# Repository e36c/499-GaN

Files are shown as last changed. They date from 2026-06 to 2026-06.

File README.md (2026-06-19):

# GaN Motor Driver
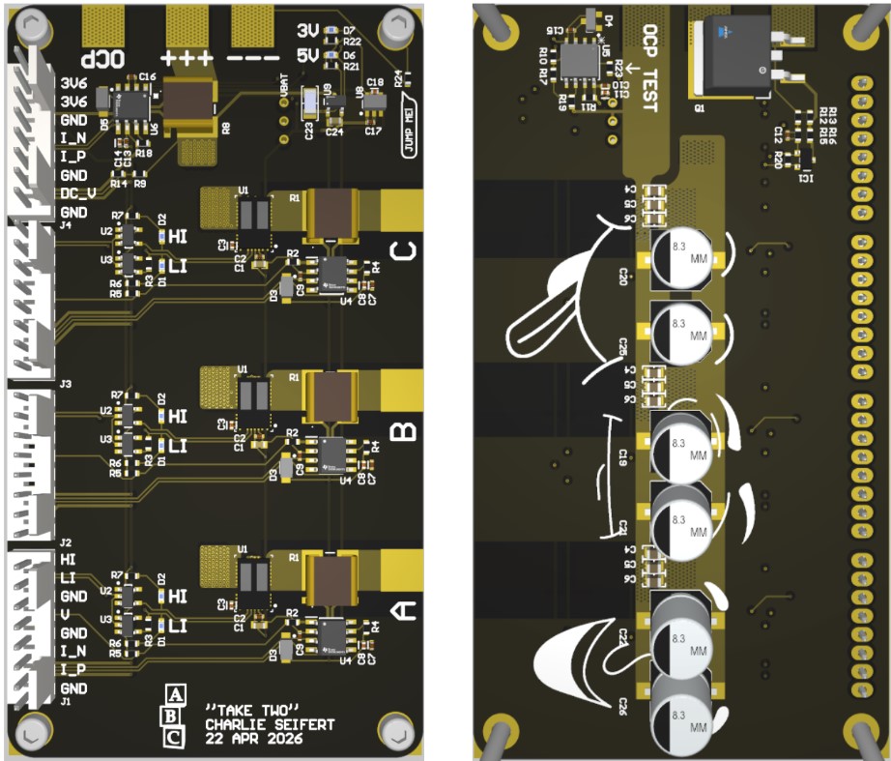
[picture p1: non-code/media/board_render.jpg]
PCB render


This repo contains the design files, code, and final report for my work on a GaN FET motor driver for an EE499 independent project with Professor Alan Sahakian at Northwestern University. All code is my own. No non-standard libraries were used, including to achieve position and speed control.

The custom PCB is capable of:
- 48 V DC supply
- 53 A phase current
- Full-range current and voltage measurements
- Running at high frequency
- Overcurrent protection

As of the end of SP26, there is code for position and speed control. This is a live repo, as I continue work on speeding up the basic control code as well as full vector control.

See [final report](non-code/final_report.pdf) for more details.

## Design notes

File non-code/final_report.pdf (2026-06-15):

Charlie Seifert
EE 499 Spring 2026
With Professor Alan Sahakian

# GaN Motor Driver

## Introduction

This report details my process for developing a custom gallium nitride (GaN) field-effect transistor (FET) motor driver. The motivation for this project was simply to learn. Though I am drawn to electromechanical systems, which a motor driver is a quintessential example of, I had a surface-level understanding of how a motor driver works and wanted to dig deeper. I also wanted an apt project through which I could learn STM32 development. I had additionally very nearly completed a similar project in Spring 2025 for Northwestern's Robot Design Studio class, and I was unsatisfied with the result and sought to finish what I had started. Given I only had one quarter to complete this project, I relied on some of the materials from the previous year's effort and clearly defined the project scope.

The goal: Develop a brushless DC (BLDC) motor driver capable of…
- 48 V DC supply
- 53 A phase current
- Current and voltage measurements to enable popular control algorithms
- Running at a very fast frequency
- Debug-friendly design
- Overcurrent protection

The main work of this project consisted of designing a single PCB that integrated the above features. A separate MCU development kit, an STM32 Nucleo board, was used to drive the custom PCB and read its output signals. The use of a pre-made development board decoupled the core low-level motor driver concepts, which were my primary concern to learn, from the potential pitfalls of integrating a bare MCU chip onto a custom PCB – no need for properly integrating a crystal, USB connectivity, etc. on a custom design. The remainder of this report will detail the specifications of the custom board, the details of my bringup process for both the hardware and software, and what the end product is capable of.

Note: This is not groundbreaking work! I did not undertake this project to advance the fields of power electronics or motor drives, nor experiment with even slightly advanced motor control algorithms. This was a personal challenge to learn how a modern motor driver works by making one myself – not one that's bleeding edge, but one that is comparable to modern options by using modern components.

### Prelude: Why GaN?

This project has its roots in a previous year's project developed for the Human AugmentatioN via Dexterity Engineering Research Center (HAND ERC) through Northwestern's Robot Design Studio class. In robotics, and especially for robot dexterity, control bandwidth is very important. Higher control bandwidth means faster responses and more natural robotic motion. The control bandwidth, i.e. how fast you can effect changes in the system, is limited by the rate at which your power electronics switch. Though I wasn't writing the control algorithms, as the EE in charge of the driver hardware, I sought to raise the ceiling for control speed as high as I reasonably could. This is where GaN, a relatively new wide bandgap semiconductor, comes in. GaN FETs have extremely low parasitic capacitance, making them capable of switching at extremely high speeds. They also come with impressively low on-resistance, meaning they can carry higher transient currents compared to traditional silicon (Si) FETs for the same transistor channel width. However, in the current state of the art, GaN FETs' thermal conductivity is slightly lower than that of Si FETs and significantly lower than that of silicon carbine (SiC), another wide bandgap semiconductor that has found its way in to many automobiles and advanced, high power density electric drives. These qualities make GaN a perfect niche for robotics: relatively low continuous power, yet still able to handle high transient currents, and capable of raising the ceiling for control algorithms by switching extremely fast. A comparison of the aforementioned three semiconductors (plus IGBTs, not relevant here) is shown below.

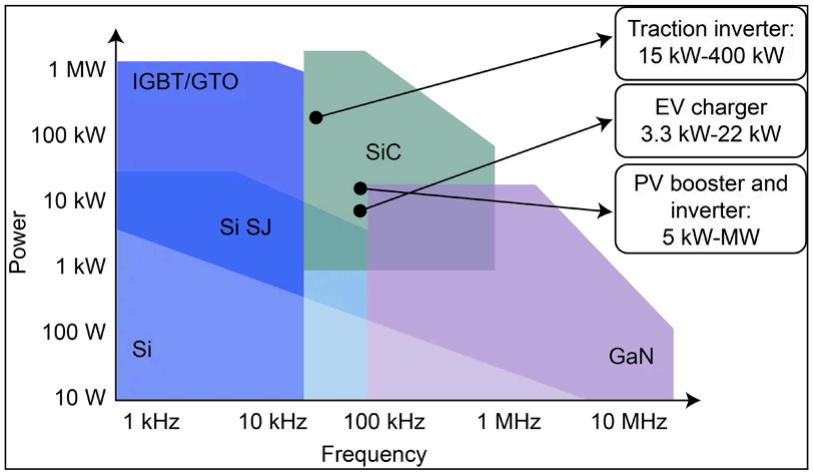
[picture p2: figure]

A comparison of IGBTs and Si, SiC, and GaN FETs. Source (https://tenxerlabs.com/resources/blogs/silicon-carbide-sic-vs-gallium-nitride-gan-right-power-transistor/)

While the potential for high switching speed is beneficial for control bandwidth, it also presents a problem: it puts pressure on the gate driver design to have very low inductance and not introduce stray capacitance that would nullify the benefits of using GaN in the first place, or otherwise produce nasty ringing that would need careful tuning. Either way, developing such a gate driver would be expensive and time-intensive, so I chose last year to rely on a chip that tightly integrated an entire half-bridge gate driver with high- and low-side GaN FETs: The LMG2100R044. (https://www.ti.com/product/LMG2100R044) This is a TI device capable of 100 V supply and 35 A phase current, and supports logic-level inputs to close the FETs. It is an amazing creation, but not without a hefty pricetag of $9.73 on DigiKey (https://www.digikey.com/en/products/detail/texas-instruments/LMG2100R044RARR/22531578) apiece in low quantities (as of June 2026). With the same tight timeline and similar goals for this year (i.e. learn about how to drive a motor, not design a gate driver), I intended to use the same chip. Upon visiting TI's website, I discovered an updated version using slightly wider GaN FETs, the LMG2100R026, (https://www.ti.com/product/LMG2100R026) which is capable of the same 100 V supply but can handle an increased 53 A continuously. I did not see a reason to limit phase current by the selection of chip, so I decided to go with the newer version at a couple dollars more apiece ($13 on DigiKey (https://www.digikey.com/en/products/detail/texas-instruments/lmg2100r026vbnr/25811484) as of June 2026).

## Requirements

Voltage: 48 V
For this motor driver to be usable, it should be built to be used with modern motors. 48 V was the highest voltage I was comfortable selecting, and most of the hobby motor world agrees – increasing your voltage capability to 48 V greatly increases your selection of high-powered motors. I found that increasing much more than 48 V did not increase selection size very much, at least up to the 100 V limit of the chip.

Phase current: 53 A
The phase current rating comes directly from the chip, as I saw no reason to limit what the chip was capable of. Besides possible trace heating for long durations of high-torque operation, everything on the board should be capable of delivering, sensing, and operating with 53 A entering or leaving any phase.

PWM frequency: ~200 kHz
This was a more vague goal, as it was less defined by hardware, and I have little experience with designing control algorithms. I at least wanted to aim higher than the traditional 10-20 kHz that almost every other commercial motor driver runs at, and I thought a 10x upgrade was worth a shot. Quite a bit of copper on the board contains signals at the PWM switching frequency, so much care was taken in layout to reduce the effects of crosstalk and both common-mode and differential-mode interference, especially on sensitive sensing lines.

Debug-friendly
This comes as a direct lesson from the previous project. Mechanical constraints were stringent enough for the prototype robotic hand in RDS 2025 that I created a very tight layout for that first iteration of GaN motor driver, which was actually a dual motor driver with 6 individual phases. It also integrated an additional stage of circuitry I called deadtime control, which enforced deadtime in hardware in case the software attempted to close both FETs in a half-bridge at once (something the LMG2100 chips do not internally prevent). Without the requirements of a larger project to meet, I was free to design this project to be much more obviously a prototype: lower-density component layout, capable of driving only a single motor, fewer components (deleted deadtime control), and more debug friendly in general, i.e. the positioning of the bulk capacitance on the bottom of the board to allow easier probing of all the smart components on the top.

Overcurrent protection
This is another requirement that came straight from the previous year's project; that board met its fate in a fiery flash after we attempted to drive it with a full motor control library without thoroughly completing prior testing. I am not sure exactly what happened, but my best guess is it was a shoot-through event caused by mistaken pins. Regardless, I sought to avoid something like that full-stop, even if I planned on being much more thorough with the hardware bringup. Built-in overcurrent protection (OCP) was the obvious answer. I designed an interesting circuit to fulfill this purpose, but at the last minute of layout I decided to relegate it to the bottom of the board and save its testing for any bonus time I might have remaining at the end of the quarter. At the time of writing this report, the onboard OCP circuit remains untested. At the advice of Professor Sahakian, I still met this goal by incorporating a good old fashioned fuse – I went through the entire prototyping process with a 100A fuse soldered inline with the DC+ connection.

## BOM

A full bill of materials for the PCB components is provided below, and can be found in the BOM tab of this spreadsheet. (https://github.com/e36c/499-GaN/blob/master/non-code/motor_driver_design.xlsx)

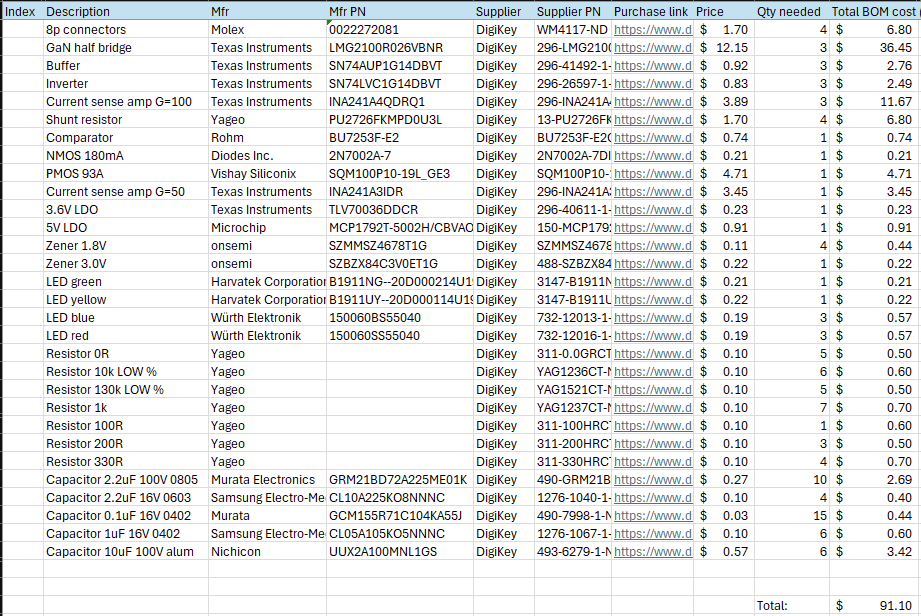
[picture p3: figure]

Bill of materials for exact quantities used on board.

## Architecture

The long-term vision I have for this project is an integrated motor drive (see H3X). (https://www.h3x.tech/) I have no hope of making anything a tenth as power dense as one of their motors, but I am very drawn to the idea of closely integrating the mechanical and electrical components of a motor into a nice neat package: DC power and control signal go in, torque comes out. Such a project would involve integrating the control side with the driver side onto a single PCB capable of mounting directly to a motor, as shown below.

The long-term goal for this project: co-package the control and drive electronics with the motor.

I wanted a stepping stone before jumping to such a constrained design, so I set my sights on a simpler architecture first: a dedicated driver board handling the fast-switching, high-magnitude voltages and currents a safe distance away from an off-the-shelf MCU development kit. A system overview is shown in the block diagram below.

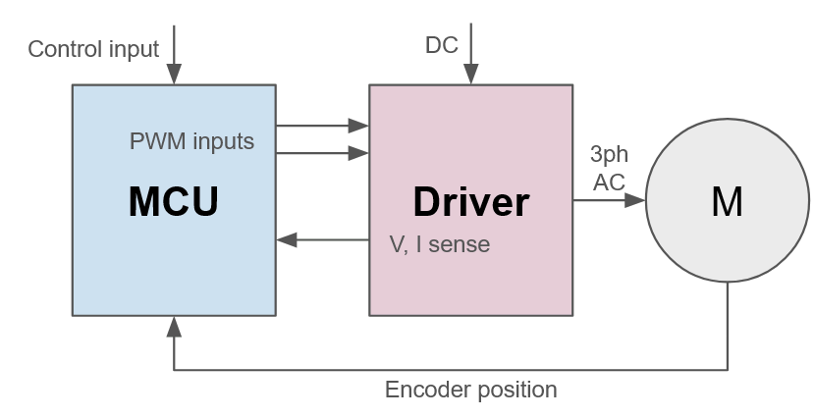
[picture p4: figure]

Simplified system block diagram. The red Driver block is what this report details.

The blue MCU block is the STM32 Nucleo board, the red Driver block is the custom PCB, and the grey M circle is a 3-phase BLDC motor. All of the early work on this project focused on the driver board: its schematic design, PCB layout, and bringup. It features inline shunt current sensing, direct voltage sensing, optional 3/6PWM input buffers, overcurrent protection, header-friendly signal connectors, simple solder pads for the high-current connections, an E-field shielding inner layer, and finally, awesome hidden graphics (you'll see). All of these features are described or shown in detail in the following two sections.

## Hardware

### Schematic

Below are the complete schematic sheets. They can be viewed in higher resolution here. (https://github.com/e36c/499-GaN/blob/master/non-code/schems.pdf)

### Overview

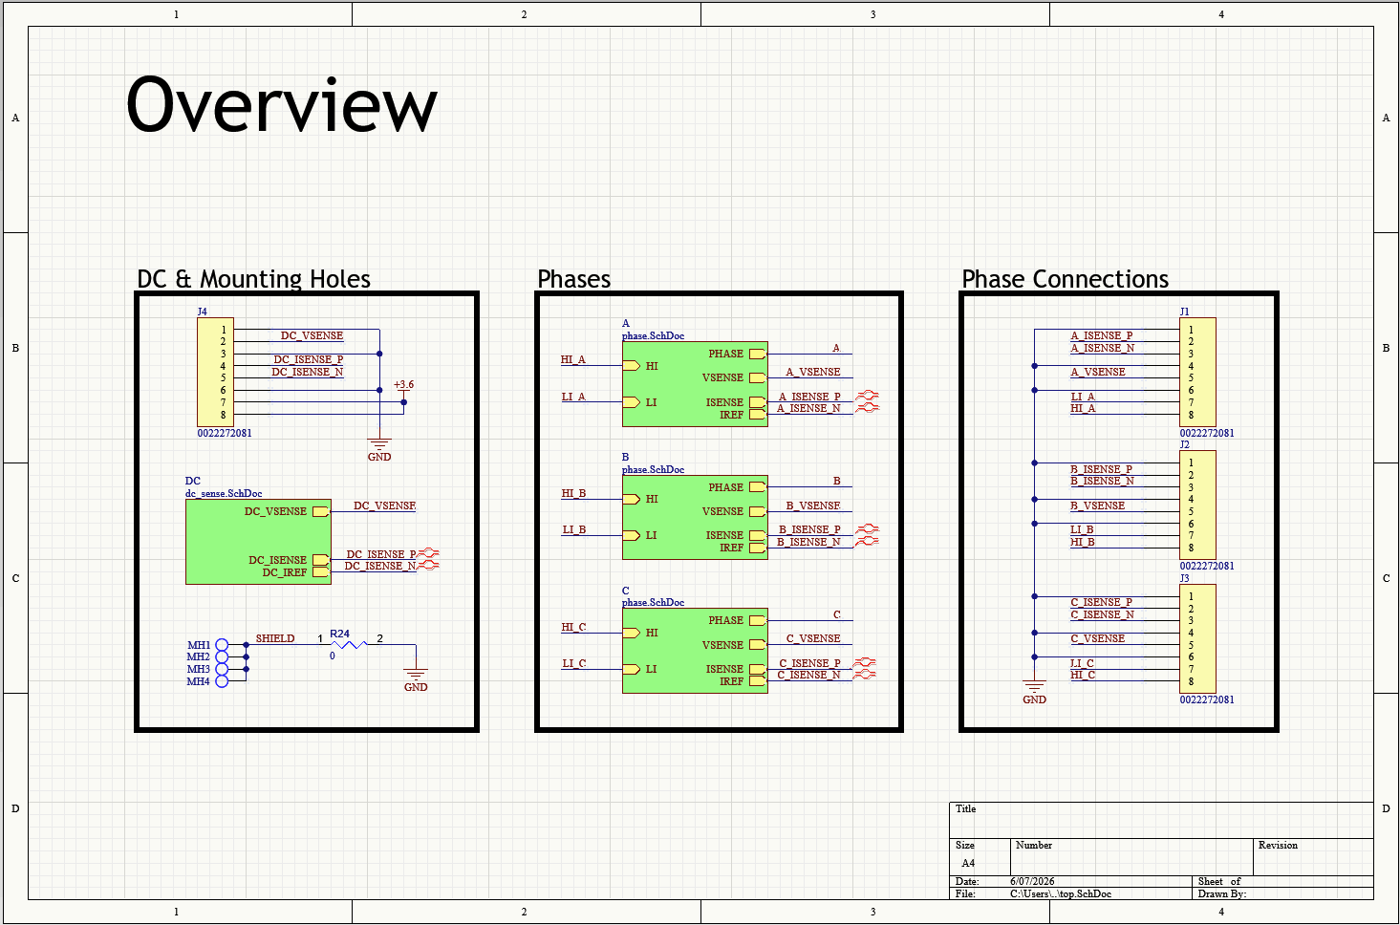
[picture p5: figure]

Overview schematic sheet.

The overview sheet includes the four signal connectors, three sets of phase circuitry, the four mounting holes and grounding, and the remainder of the board's components under the "DC" block.

- Green blocks represent other schematic sheets, and the inlaid yellow arrows their connectivity. You will see the corresponding yellow arrows on the following schematic sheets.
- The decision to use four signal connectors came from a desire to have three identical connectors, one for each phase, and the remainder of the signals (loosely referred to as "DC") were grouped into a fourth. They neatly fit on one side of the board within dimensions I was comfortable with.
- The four mounting holes are tied to GND via 0R jumper R24 because they connect to a specific inner shielding layer. Directly assigning the GND net to the mounting holes and shield layer would have caused all four mounting holes, as well as many GND vias (!) to be directly connected to the shield. Conventional EMC wisdom states that shielding of that kind should be connected to ground in exactly one place to prevent ground loops and generally improve ground quality; the way I achieved this sort of connectivity in Altium without making a thousand design rules was by using a jumper to separate the two nets – I was quite happy with this solution, provided I had the available board real estate.

### Phase

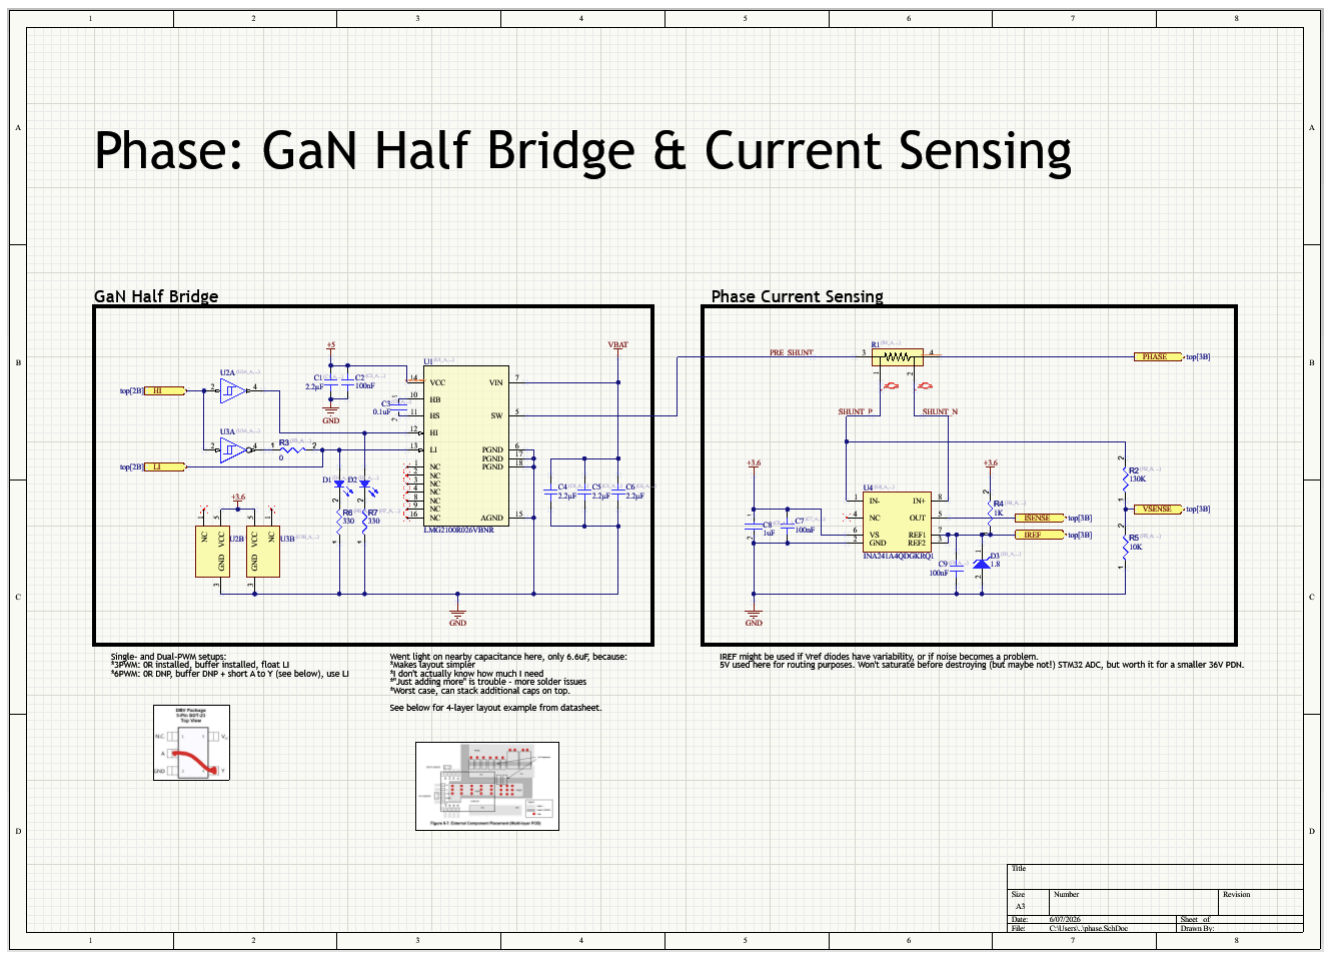
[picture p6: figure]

Phase schematic sheet.

The phase sheet is where the most "motor driver" components lie: The half-bridge module and surrounding circuitry, plus the inline shunt current sensing.

- The half-bridge chip integrates so much that about the only thing needed to support it are capacitors. All of them were deliberately chosen, particularly their construction, value, and package:
- C1 and C2 are ceramic decoupling capacitors to filter noise of differing frequencies off of the 5 V rail, which supplies the LMG2100's internal circuitry (UVLO, level shifting, etc.).
- C3 is the bootstrap capacitor. TI explicitly recommends a ceramic 0.1 uF 0603 for this purpose, and to closely locate it to the HS and HB pins of the chip. Note that without an isolated supply like you might see in higher-power motor drivers, this capacitor is what supplies the gate of the high-side FET with sufficiently high voltage to switch DC+ to the switch node. See page 11 of the LMG2100 datasheet. (https://www.ti.com/lit/ds/symlink/lmg2100r026.pdf)
- C4, C5, and C6 are 2.2 uF 0805 ceramic capacitors that provide some of the bulk capacitance that is recommended for supplying current in high transients. These have lower parasitic inductance than the wound aluminum electrolytics shown on the next sheet, which makes them great at handling higher frequency transients.
- A buffer and inverting buffer are fed by the HI input.. They allow what is called a "3PWM" configuration, where only three PWM outputs are needed to drive the half-bridges. This saves pins on the MCU at the cost of a fixed dead time and no option to completely open each half-bridge; 3PWM means that one switch of each half-bridge will always be closed. The alternative is 6PWM, which would be configured by depopulating jumper R3 and the buffer, then shorting input to output across the buffer's footprint as shown in the schematic sheet.
- LEDs were included on the HI and LI inputs, which are the logic-level inputs that close the high- and low-side switch, respectively. This was done for debugging, and proved very helpful as a reliable sanity check. Effects of added capacitance on these lines from the diodes are not exactly known, but assumed to be negligible at feasible PWM frequencies.
- The right side of the sheet shows the two major components of each phase's current sensing circuitry: the shunt resistor and the amplifier. The shunt resistor sits inline with the high current path so that the voltage it drops is readable as a differential voltage by a differential amplifier. This means it must be very low value to avoid wasting power. This then means that the amplifier must be high gain – it was chosen to be 100 (see section below for calculations). The amp must also be capable of rejecting common-mode voltages quite well, as the common-mode voltage the resistor sees wildly fluctuates with the switching of the half-bridge. More on that later.
- A zener diode supplies the reference voltage that the amplifier adds its reading to; a reference voltage greater than zero allows bidirectional current sensing. The value of 1.8 V was chosen to be right in the middle of the STM32 ADCs' max input voltage of 3.6 V, which is also what the amplifier gets supplied so that it may never exceed the STM's max rating. Being in the middle of the range maximizes measurement range of positive and negative current, which we expect to be symmetrical.

- The resistor inline with the zener diode was selected to be too low; the reference voltage is quite a bit higher than 1.8 V with a 1 kR.
- Voltage sensing is implemented with a simple resistor voltage divider.

### DC Input

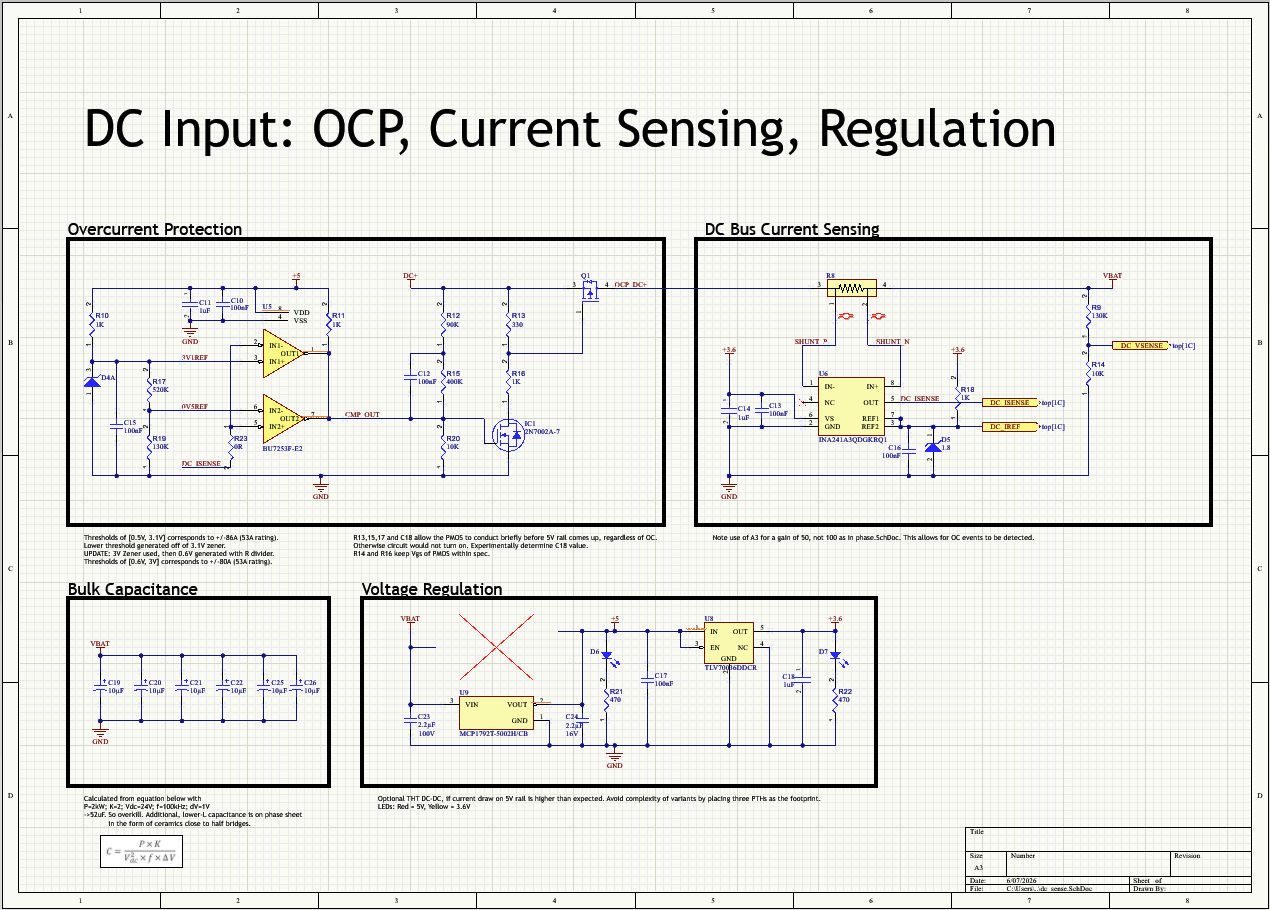
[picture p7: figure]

DC input schematic sheet.

The DC input sheet contains the rest of the board's circuitry: OCP, DC bus current sensing, bulk capacitance for the half-bridges, and voltage regulation.

- OCP is a doozy – see full section below.
- DC bus current sensing is largely the same as the phase current sensing, albeit with an amplifier with a gain of only 50, not 100. This allows for twice the range of current sensing, mainly for the purposes of sensing an overcurrent event. This hurts resolution, but DC current is usually not used by control algorithms that would benefit from accuracy.
- The bulk capacitance is made of high-valued aluminum electrolytic capacitors that take up the remainder that the 2.2 uF ceramics on the phase sheet don't cover. See layout for how these are distributed underneath the three half-bridges. See calculations in section below.
- Voltage regulation simply takes in the input voltage and regulates it down to 5 V and 3.6 V. 5 V is used exclusively for the comparators and the half-bridges, the latter of which require it for their internal circuitry. 3.6 V supplies everything else: the buffers, current sense chips, zener diodes, and the STM32 board if not externally supplied.

### Major decisions

### Bulk capacitance

This equation for DC link capacitance (from this article (https://www.chinajiangsen.com/news/Blog/DC-Link-Capacitor-Calculation-for-Inverter.html) on inverter design) was used to estimate the amount of bulk capacitance to place across the supply rails:

C =

P×K
V
DC

×f×∆V

The meaning and values chosen for each parameter is given in the table below.

Parameter | Meaning | Value chosen | Justification
P | Power | 2000 W | In the ballpark of 48 V * 53 A = 2544 W
K | Voltage ripple tolerance, typically [1, 2] | 2 | Low voltage ripple tolerance; conservatively oversizes C
VDC | Supply voltage | 24 V | Though the board can support 48 V, this conservatively oversizes C
f | Switching frequency | 100 kHz | Aiming for a higher figure, so this conservatively oversizes C
ΔV | Allowable voltage ripple | 1 V | 2% of 48 V

Given these parameters, the resulting bulk capacitance is 69.4 uF.

I assumed that each phase could make use of all of the large electrolytic capacitors, but only the close-by ceramic capacitors. Therefore, capacitors with the following parameters were chosen.

Capacitor type | Package | Value | Quantity | Total capacitance per phase
Electrolytic | Radial can | 10 uF | 6 total | 60 uF
Ceramic | 0805 | 2.2 uF | 3 per phase | 6.6 uF

This makes the equivalent total bulk capacitance available to each phase 66.6 uF, which is 96% of the calculated value of 69.4 uF. I deemed this good enough given my conservative sizing calculation.

### Current sense

Inline phase current sense circuitry requires high-quality components. The differential amplifier has the most important job: Convert a small voltage across a resistor to a cleanly amplified output without including common-mode voltage, which wildly flies around because of how fast the half-bridge is being driven. The requirements for the current sense circuitry are:
- Sense at least 53 A
- Don't amplify noise
- Output remains within 0 to 3.6 V (STM32 ADC max input voltage)
- Not exceed shunt resistor's power rating

I decided to keep my choice of amplifier from last year's project, the INA241. It is a remarkably flexible family of devices: They are the state of the art in current sense amplifiers: they can take as high as 20V supply, have an extremely low common-mode rejection ratio (CMRR), come in a range of fixed gain options, and are easy to design around. Note that two different gain options were used for each of the phase current sense circuit and the DC current sense circuit: 100 and 50, respectively, to allow for overcurrent detection on the DC line. The "Current Sensing" page of this spreadsheet (https://github.com/e36c/499-GaN/blob/master/non-code/motor_driver_design.xlsx) supported my search for a combination of gain choice and shunt resistor. I did not pay much mind to the power lost across the shunt resistor beyond whether or not it was within the device's rating. The final shunt resistor, the Yageo PU2726, (https://www.digikey.com/en/products/detail/yageo/PU2726FKMPD0U3L/25854094) has the below specifications.

Shunt resistor spec | Nominal value
Value | 0.3 mOhm
Power | 11 W

The final spreadsheet after selection of the shunt resistor is shown below. It accounts for component variation and indicates (with a green highlight) when output parameters are desirable or within the given shunt ratings. All important parameters of the current sense circuit are shown.

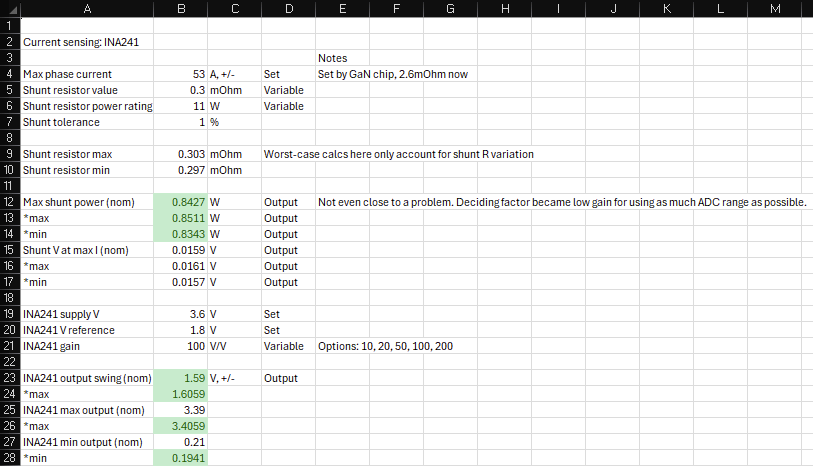
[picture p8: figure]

Spreadsheet that aided in shunt resistor selection.

### 3PWM buffer and inverter

To allow for more flexible usage of MCU pins, I designed the board so that each phase could be driven with one or two PWM channels. The use of two PWM channels per phase is called 6PWM, and the use of one is called 3PWM. 6PWM allows the most control over the closing of each side of the half-bridge at the cost of three additional MCU pins. 3PWM simplifies pin usage by always closing one side of the half-bridge: a logic HIGH closes the upper switch, and a logic LOW closes the lower switch. This channel would directly drive the input for the upper switch, while its inverse would drive the input for the lower switch. Therefore, a digital inverter is used to invert the 3PWM channel to drive the lower switch. I added a buffer before the input to the upper switch to try to compensate for the delay added by the inverter. Close attention was paid to the propagation delays of these devices, since that parameter would 1) add latency to inputs and 2) cause problems if mismatched. The details of chosen two parts are given in the table below for room temperature operation at as close to 3.6 V supply as they list.

Part | Datasheet | tpd (max, min) (ns)
SN74AUP1G17 (buffer) | Link (https://www.ti.com/lit/ds/symlink/sn74aup1g17.pdf) | 2.2, 5.7
SN74LVC1G14 (inv. buffer) | Link (https://www.ti.com/lit/ds/symlink/sn74lvc1g14.pdf) | 1.8, 6.5

To use 3PWM, all devices in the half-bridge portion of the Phase schematic sheet are to be installed on the board, and the LI input is to be left floating. If 6PWM is to be used, the hardware can be reconfigured in the following way:
- Do not populate R3
- Do not populate buffer IC

- Short the input and output pads on the unpopulated buffer footprint

Since my pin budget allowed for it through all stages of testing, I opted to use 6PWM along with complementary PWM generation that the STM32 supports. This feature allows simple programming of dead time, which I would not be able to control with the simple design I chose to support 3PWM.

### Overcurrent protection

A blow-up of the overcurrent protection circuit schematic is shown below.

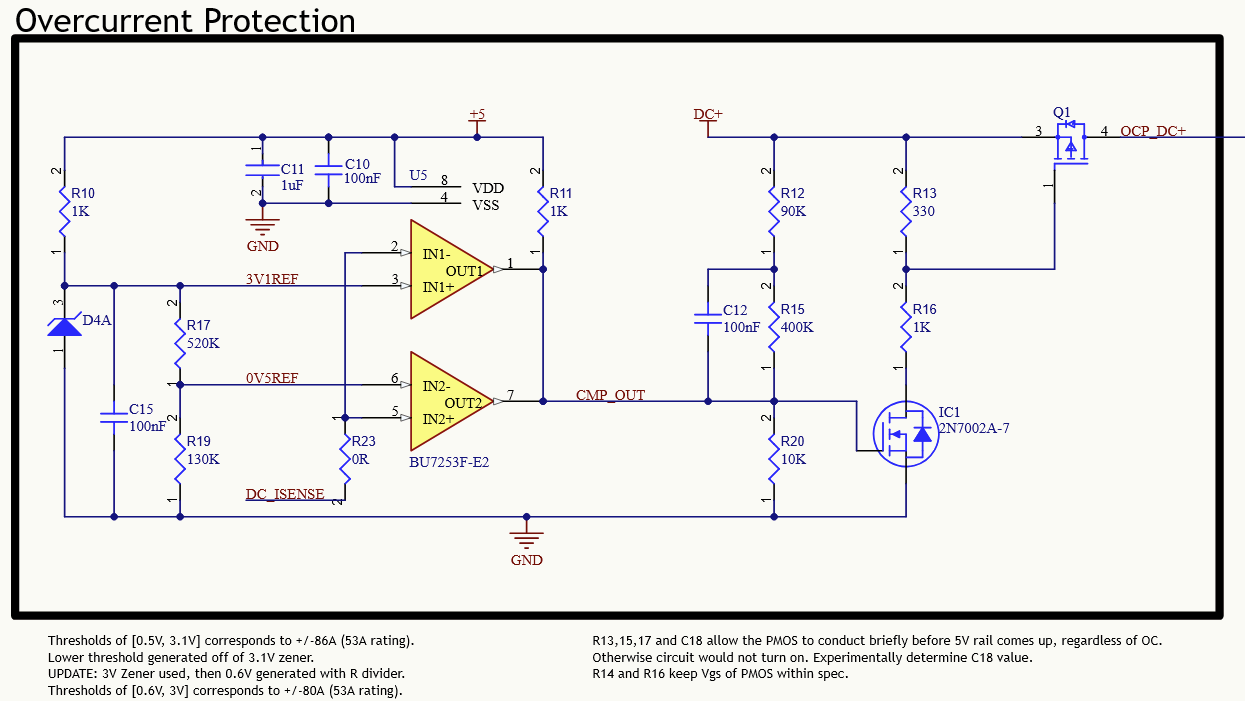
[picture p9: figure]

Overcurrent protection circuit.

This circuit simply opens a Si PMOS inline with the main supply line when it detects an overcurrent condition. Detection is done by running the output of the DC current sense circuit through a window comparator, which then drives a Si NMOS to switch the gate of the PMOS. A resistor network is used in the right-hand side of the schematic to meet Vgs ratings of both FETs, as well as to create a "power-on reset" effect. This power-on reset effect is achieved with a simple three-resistor voltage divider with a capacitor across the middle resistor. Assuming the capacitor is discharged, the output of the circuit (which is the NMOS gate connection) will gradually change from a higher voltage to a lower voltage, meaning the circuit will always attempt to close the PMOS on startup. Otherwise, I theorized (though never experimentally verified) that the PMOS might never close at all, and our overcurrent protection would be so good at its job so as to never allow any current to flow. This was designed to work with both 24 V and 48 V supplies. Low-valued resistors were used to ensure that the turn-off time of the PMOS, given by the RC circuit of R16 and the gate capacitance, kept the switching loss within the device to within its dissipation rating. The below slide I created at the time of designing this circuit shows all the math involved to arrive at this answer.

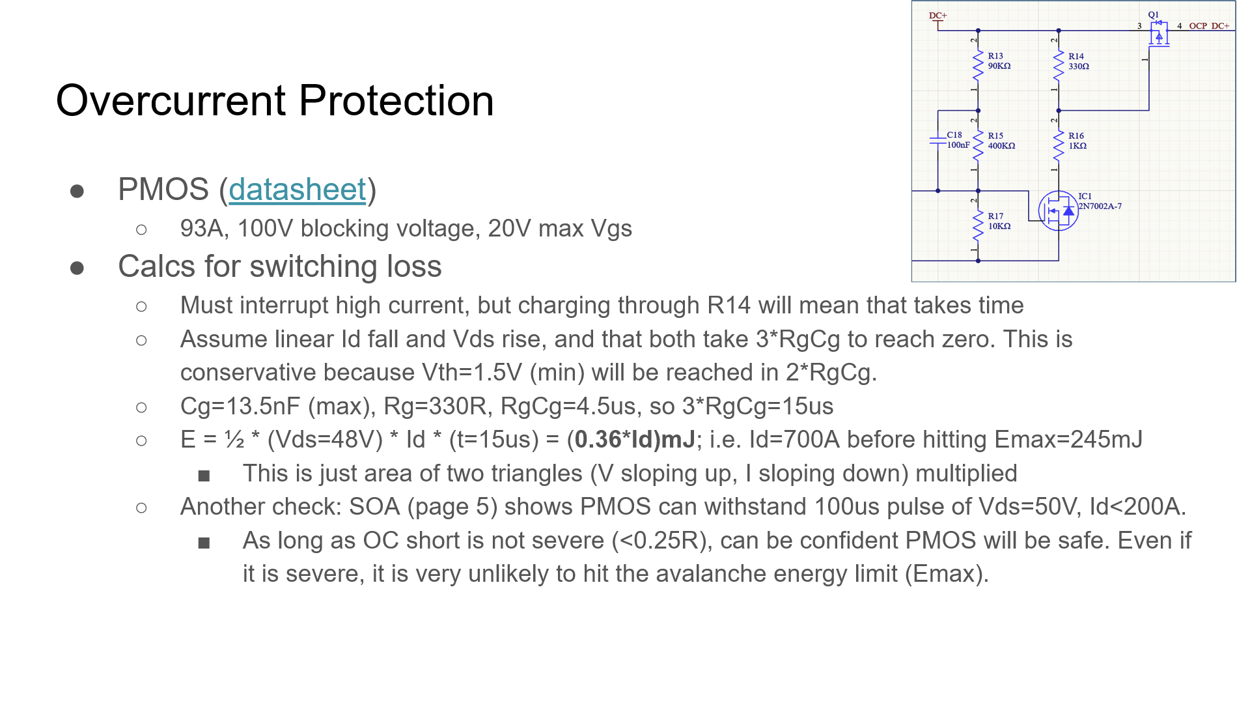
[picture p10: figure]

Math and justification for PMOS switching loss when overcurrent condition is met, given RC circuit created by R16 and the gate capacitance of the PMOS.

### Power regulation

I made a design decision that might seem suspicious at first glance: all voltage regulation on the board is done with low-dropout linear regulators, or LDOs. This was done very simply because the power draw on the two required voltage lins was low enough that the simpler integration and less noisy output of an LDO won over the higher integration cost of a switching regulator. The tables below give conservatively high estimates for the current draw on each voltage line, using information from each device's datasheet; note that current draw from high-impedance voltage dividers and the like was considered negligible.

Current draw on 3.6 V line

Device | Est. current (mA) | Quantity | Total current (mA)
Buffer | 1 | 3 | 3
Inverter | 1 | 3 | 3
Current sense amplifier | 2.5 | 4 | 10
Zener diodes | 1 | 4 | 4
Power LED | 5 | 1 | 5
| | Total: | 25

Current draw on 5 V line

Device | Est. current (mA) | Quantity | Total current (mA)

GaN half-bridge | 5 | 3 | 15
3.6 V line draw | 3.6/5 * 25 =18 | 1 | 18
| | Total: | 33

Also note that the input current to an LDO is given by the product of the output current and Vout/Vin

My final selection for the two LDOs as well as some of their specifications are given in the table below.
Part | Datasheet | Vin range (V) | Max Iout (mA)
TLV70036DDCR (3.6 V) | Link (https://www.ti.com/lit/ds/symlink/tlv700.pdf) | [2, 5.5] | 200
MCP1792T-5002 (5 V) | Link (https://ww1.microchip.com/downloads/aemDocuments/documents/APID/ProductDocuments/DataSheets/MCP1792-Family-Data-Sheet-DS20006229D.pdf) | [4.5, 55] | 100

Note that the 5 V regulator feeds the 3.6 V regulator.

Just in case I was somehow very wrong in this analysis, I included three plated through-holes connected, spaced, and sized properly to allow the installation of a TSR 2-2450, (https://www.tracopower.com/products/tsr2.pdf) a fully-integrated 5 V DC-DC converter I had experience with, in parallel with the 5 V LDO. This device can output as high as 2 A, which I deemed more than enough.

### Layout

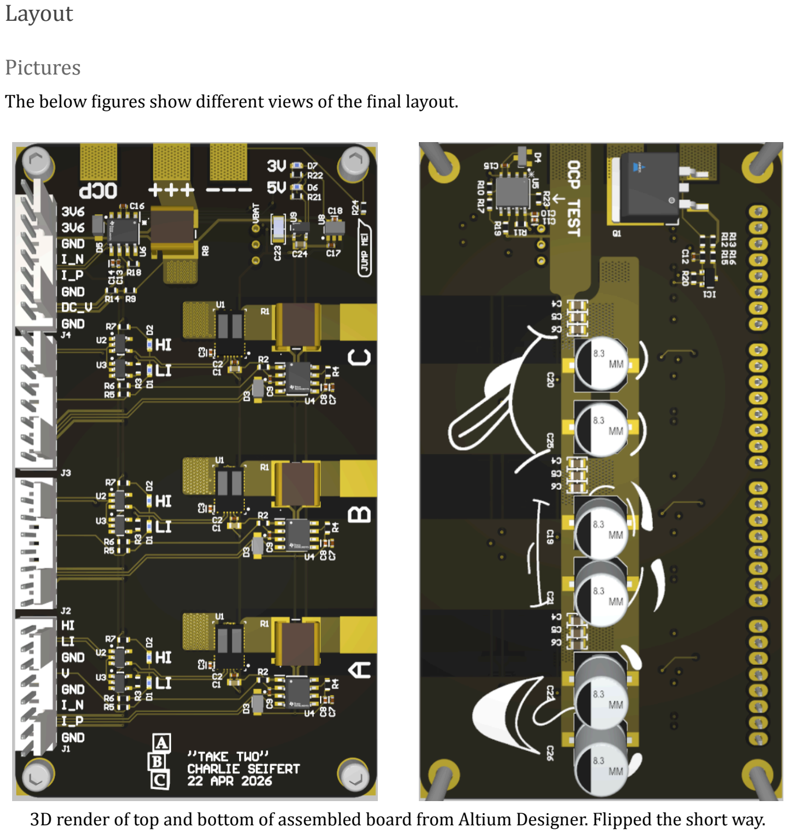
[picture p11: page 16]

### Pictures

The below figures show different views of the final layout.

3D render of top and bottom of assembled board from Altium Designer. Flipped the short way.

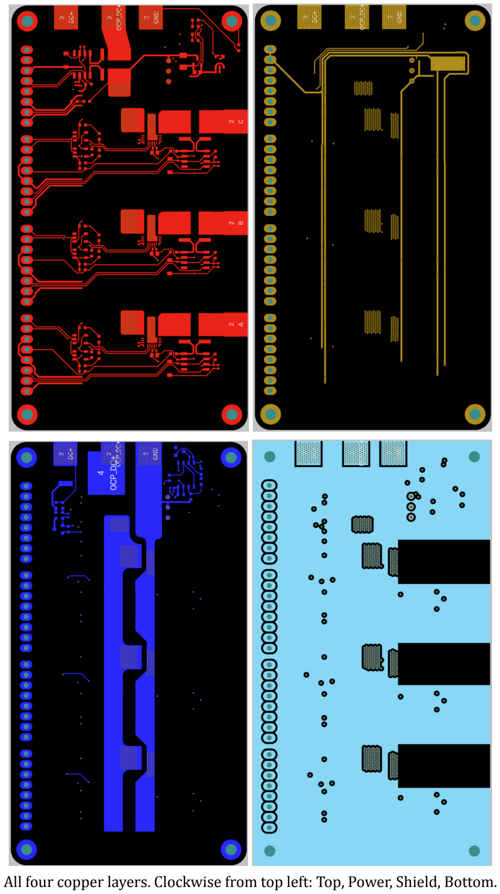
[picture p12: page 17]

All four copper layers. Clockwise from top left: Top, Power, Shield, Bottom.

### Goals

Following the requirements for this prototype, the two big priorities for the layout were being debug-friendly and maintaining signal integrity. The high-level decisions that each of these priorities led to are given below.
- Debug-friendly
- Space out components
- Large capacitors on bottom
- Exposed vias for probing
- Normal breadboard-style male headers
- Signal integrity for sensitive measurements
- Differential routing of current sense lines, PWM input lines
- Sensitive signals cross power planes perpendicularly
- Shielding traces adjacent to sensitive traces
- Shield layer

The previous year's board was too dense for a prototype. The initial assembly did not go smoothly, as a slightly heavy solder paste application caused shorts that were very difficult to debug due to the density. This year, I made it a priority to make the board more debug-friendly. It already helped that I only cared to control a single BLDC, not two like the previous project. The layout therefore only crams devices together if it is obviously beneficial for them to be so. This led to a layout strategy of clumping together devices only where needed, then using more real estate in connecting those clumps together, following the theory that the less dense the board is, the easier it is to debug. You can also see that even within clumps, any two devices are often not crammed super close together and maintain some breathing room to limit the odds of a short during assembly, and to allow for easy probing.

Noisy measurement signals would worsen the performance of certain control algorithms, making it harder to know if the algorithm is the problem and not just signal noise. This led me to give quite a bit of thought to how to route sensitive signal lines, particularly the current and voltage readings. The lines from the shunt to the amplifiers are a good example; any noise that couples into them would be amplified before going back to the MCU. Therefore these lines are very short. Differential routing for the post-amp current sense lines means that common-mode noise affects both signals simultaneously, and I laid out each phase connector to allow for ADC reading of both sides of the differential signal. Perpendicular crossing of these lines limits crosstalk by maintaining orthogonality between the two conductors' magnetic fields. The shield layer keeps the fast changing E-field present on the two long pours of the DC bus on the bottom layer from affecting the sensitive signal copper on the top.

### Overview

The board has four layers. The high-power pours reside on the top and bottom layers, with the top holding the DC input and output phase pours, and the bottom holding the main strip of DC+ and DC–. This was done because the bulk capacitors reside on the bottom of the board, which was in turn done to make the geometry more favorable and because it would make probing the top side of the board easier. The inner layers respectively carry the routing of power and ground, and a shielding layer. The full stackup information is shown in the figure below.

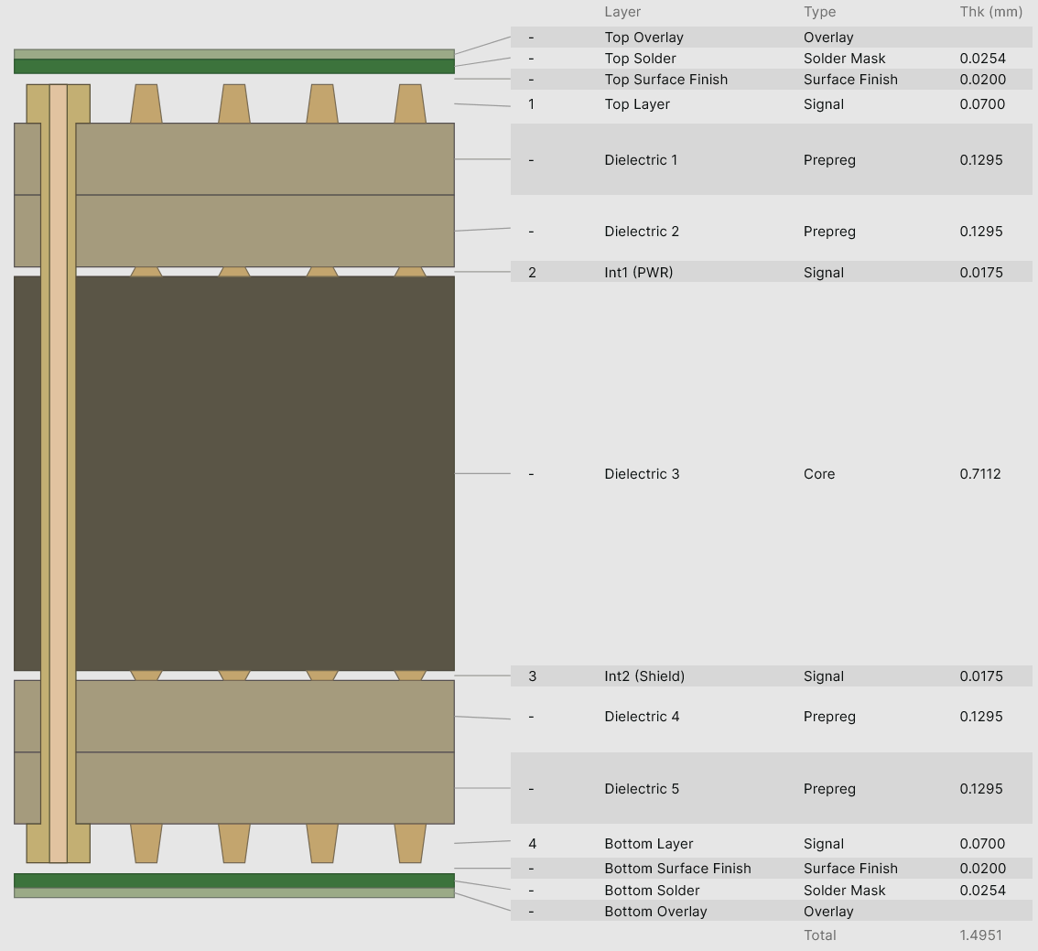
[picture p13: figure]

Layer stackup from Altium Designer. All of these are default options for a four-layer board, except for the thicker top and bottom copper layers, which were 2oz.

The board is organized into three main sections:
- Phases (3x: A B and C)
- Input buffers
- PWM indication LEDs
- GaN chip and accompanying capacitors
- Current sensing
- DC input
- DC current sensing
- OCP circuitry (bottom)
- Voltage regulation
- 5 V and 3.6 V LDOs and accompanying capacitors
- Power indication LEDs
- Through-holes for optional 5 V DC-DC
- Jumper to connect SHIELD to GND

These sections are indicated in the figure below.

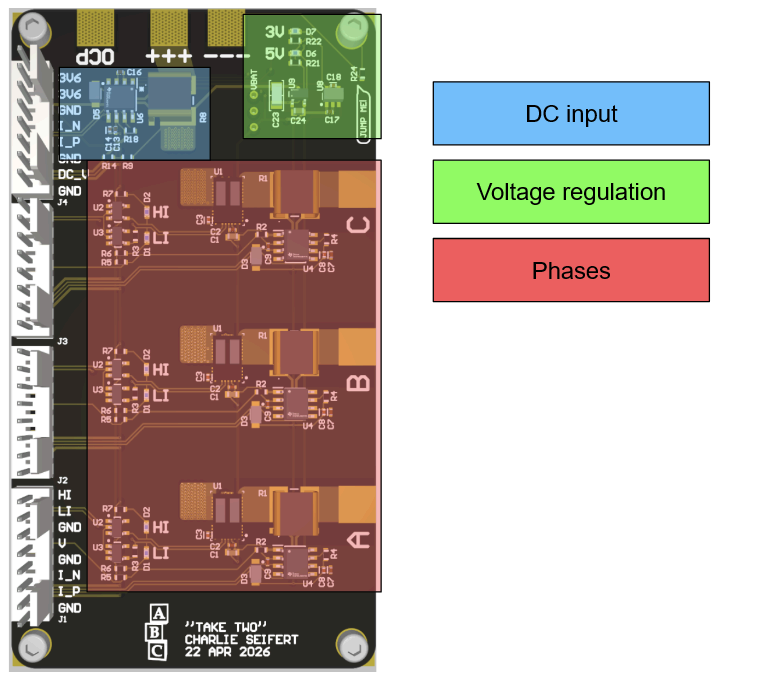
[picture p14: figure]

Sections of the board layout.

Note the presence of an additional solder pad titled "OCP"; this pad is switched to the "+++" pad (itself accessible to allow the bypassing of OCP) via the PMOS that the OCP circuit opens when it detects overcurrent. In the single prototype I assembled, I did not install any of the OCP circuitry and connected the DC input across the "+++" and "–––" pads, which I will refer to as DC+ and DC–. The DC– net immediately vias to the bottom layer, where it connects into a long pour that ties into the bulk capacitors for most of the length of the board. It also ties into the board's signal GND at a single point. The DC+ net goes through a shunt for DC current measurement, then vias to the bottom layer to connect into a similar pour for the bulk capacitors. Careful attention was paid to make sure the vias on these pads were untented on the top and tented on the bottom. The large electrolytic capacitors on the bottom are placed in pairs between the GaN chips on the top, allowing for large sections of stitching vias to be placed partially in the pad of the GaN chips to connect to the long DC+ and DC– pours. (This also presented an irresistible anthropomorphizing opportunity – their names are Craig, Bon, and Alan.) Note that all bulk capacitance is on the underside of the board. This adds some undesirable inductance to the power loop of the GaN chips, but it is not so bad, as evidenced by the TI-recommended layout strategy for a 2-layer board using the chips below.

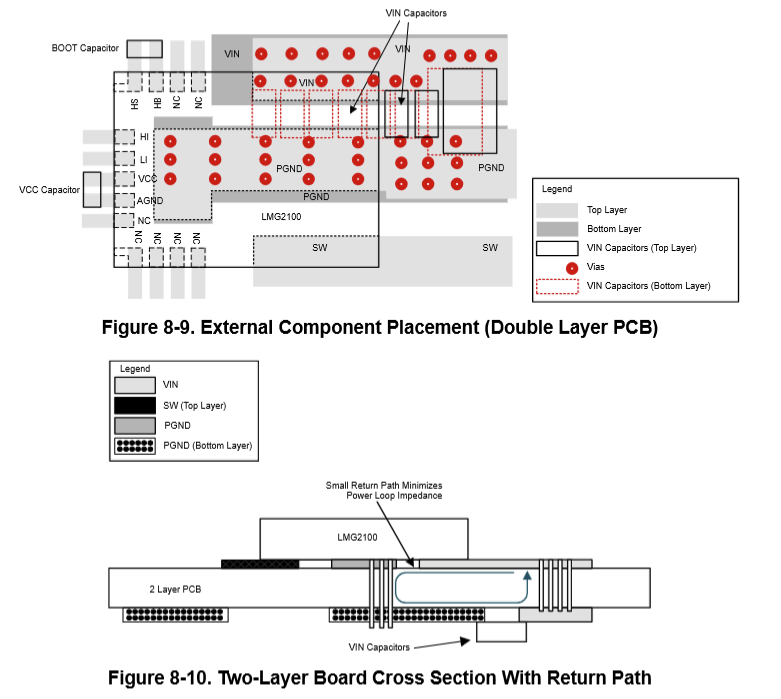
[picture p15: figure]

Recommended layout strategy for bulk capacitance ("VIN Capacitors") for a 2-layer board.

The three phase layouts are basically identical. The buffer and inverter drive the inputs of the GaN chip, then copper pours connect the half-bridge chip to the shunt to the output solder pad. The current sense amplifier and accompanying passives are placed close to the shunt to minimize noise coupled into the amplifier inputs. Many stitching vias connect between the large copper pours carrying high currents.

The voltage regulation section is nothing special. A small GND pour underneath the LDOs is present to allow easy for easy vias. Routing of these power domains required a bit of deliberation, as it was going to be difficult to reach the current sensing circuitry with a clean power line (which could have been 5 V or 3.6 V, given the wide input supply range for the INA241) and signal GND, as well as GaN chip 5 V pins. Since the GaN chip definitely needed 5 V, and I could reach their pins relatively easily with a horizontal trace (perpendicular to the high-dI/dt outputs switch nodes),

The board was manufacturing using JLCPCB. The manufacturing parameters for the board are given in the figure below.

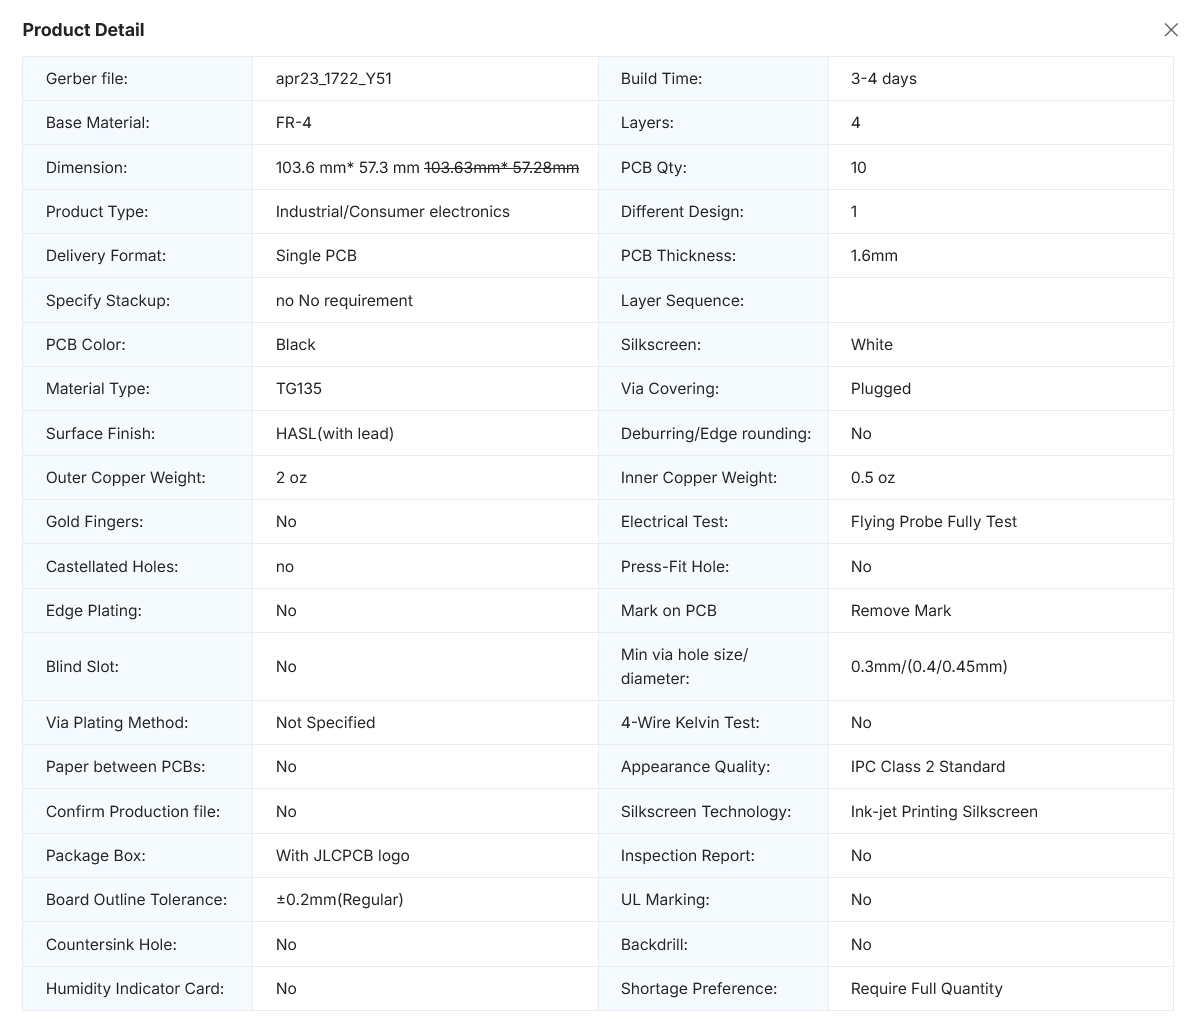
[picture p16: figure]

Manufacturing options selected for production at JLCPCB.

## Mechanical design

The encoder and the diametrically-magnetized magnet attached to the rotor had to be rigidly co-located. A single, simple 3D print did the job. The CAD is shown in the screenshot below.

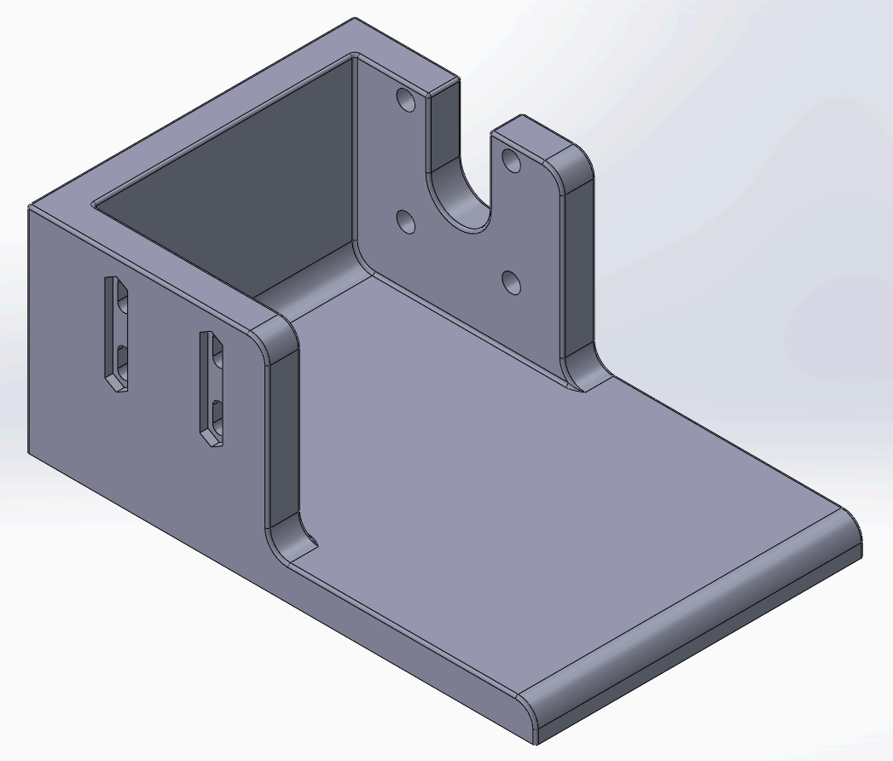
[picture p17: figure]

Motor mount CAD. File available here. (https://github.com/e36c/499-GaN/blob/master/non-code/motor_mount.SLDPRT)

It has the hole pattern for the motor’s mounting holes and vertical slots for the encoder’s, allowing vertical adjustment of the encoder. Recessed, wider slots on the outside of the encoder mounting slots made assembly a bit easier. The motor’s hole pattern was incorrect, and I had to drill different holes - there was no official CAD for it and I must have measured the hole distance wrong. The mount was designed to have the wires from the motor leave out of the top and the motor viewable from the front, so it can be easily installed and viewed. Finally, a plate extends out from the front of the model, providing a nice surface to clamp the whole assembly securely to a table when testing. This design worked great: it was plenty thick to hold everything securely, the vertical adjustment of the encoder came in handy, and I didn't have to hold a small M2 nut due to the hexagonal slots. After assembly, the spacing between encoder and motor was a little tight, as I measured the thickness of a axially-magnetized magnet as opposed to a diametrically-magnetized magnet, but that is the only thing I would change.

## Software

### MCU selection and toolchain

One of the main things I was excited for with this project was to get experience with STM32 development. STM32 is a family of 32-bit microcontrollers from ST Microelectronics popular for its wide range of device capabilities, high performance, and ease of development. I had overseen a couple really awesome projects using STM32 MCUs during my time on Northwestern's Formula SAE team, and I was happy that this project presented an opportunity to get hands-on with one myself.

Buying an off-the-shelf development kit ("devkit") was a no-brainer for the goals of this project. ST calls their devkits Nucleo boards. I sought a Nucleo that used an STM32F4 chip, which is the highest-performance of their already high-performance F line. I had heard of it being used in other demanding motor control applications, and at the risk of sounding like a broken record, I had no intention of limiting performance of my board due to MCU selection if it was reasonable to acquire one. I settled on the STM32F446, for no reason greater than its availability and fast shipping on Amazon.

Another no-brainer was the use of ST's own STM32 development toolchain, which uses two applications: STM32CubeIDE ("CubeIDE") and STM32CubeMX ("CubeMX"). The former is the IDE where you spend most of your time writing C/C++ code and running the very capable debugger, and the latter is an extremely handy program that enables super simple graphical setup of programs requiring certain peripherals. These programs work together nicely to make any changes – whether low-level logic changes to the code or higher-level modification to peripheral setup – very simple.

### Peripheral bringup

My general approach to development for this project was to heavily rely on the STM32F446's highly capable peripherals and minimize the complexity of code written by me. I anticipated that this strategy would make debugging the project simpler without limiting the capability of my programs, as my goals did not include making highly sophisticated or advanced control algorithms. In particular, my STM32 MCU makes direct memory access (DMA), which enables peripherals nad memory to exchange data without the need to do so explicitly in the main loop, very simple to use, and it can be used with basically every peripheral I could ever find the need for. This also supports my goal of enabling fast control, as you don't have to spend as much CPU time doing variable assignments.

The basic peripherals that form the building blocks of the sort of simple-yet-advanced motor control program I was looking to write were:
- Analog-to-digital converter (ADC)
- Pulse-width modulation (PWM)
- Serial-peripheral interface (SPI)

The following sections detail my bringup process for each. The below figure serves as a visual reference for which pins each peripheral was assigned to on the STM32F446 64-pin package. Note that this pin layout was carefully decided to be able to be replicated on a custom PCB in the future.

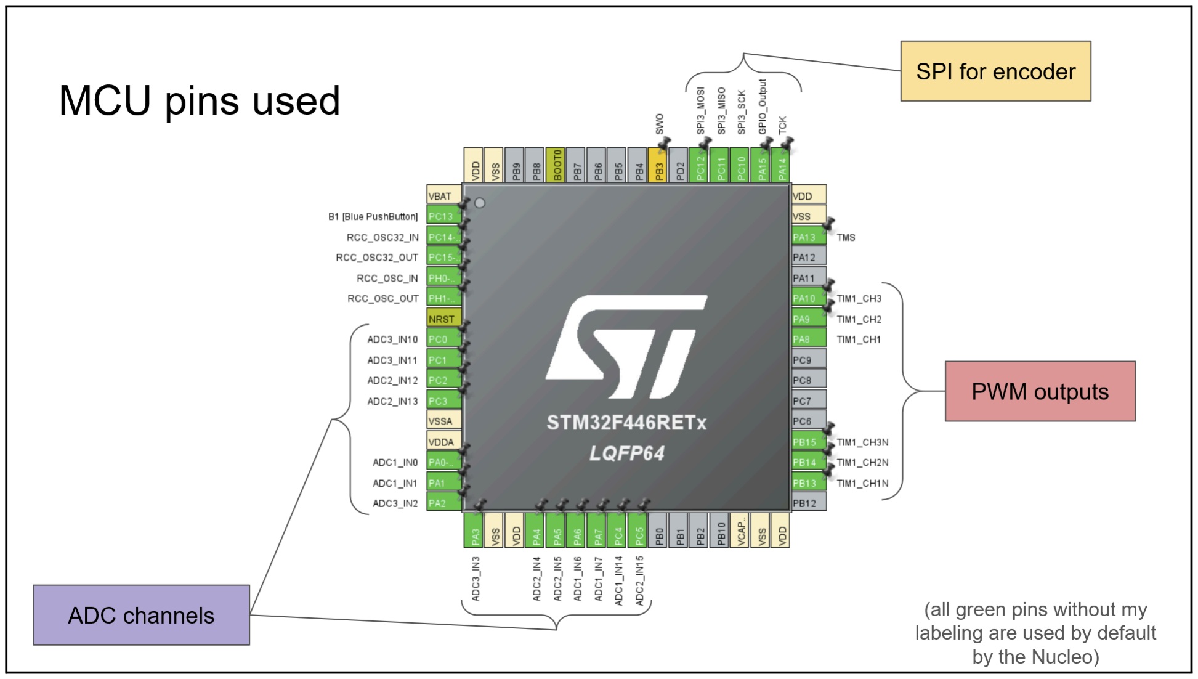
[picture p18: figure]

Pin assignment for the three peripherals I used.

### Analog-to-digital converter

My first goal with my new STM32 devkit was to investigate how the ADC peripheral worked. For my first actual program (beyond the basic blinky to validate the toolchain and board worked alright – they did), I ran a program that used just one channel of one ADC. Once I got that working, I wanted to take a step closer to how I would actually be using the ADC peripheral, with many channels being used. One good thing about the STM32F446 is its three independent ADC modules, which you could configure to simultaneously sample three separate voltages at once. This is explicitly advertised to be used in motor control algorithms, where you want to be sure that all current measurements are made at the same time because phase currents can change quickly. As shown in the pinout figure above, I needed a lot of ADC readings. In groups of which should be simultaneously sampled, these were:
- Phase current sense measurement (3x)
- Phase current sense reference (3x)
- Phase voltage sense measurement (3x)
- Phase voltage sense reference (3x)
- DC current sense (1x)
- DC voltage sense (1x)

This totals 14 ADC readings I wanted to make, requiring 14 ADC channels configured through STM32CubeMX. I grouped them into groups of 3, sampled in the order given in the above bullets. I grouped DC current and voltage sense together, then threw in a repeated channel in with them to make an even 5 sampling events of 3 voltages. I configured DMA to place all 15 readings into a buffer called adc_dma_buffer.

Some subtleties in peripheral setup caused some hiccups initially. One was caused by the fact that I tried to do continuous conversion and then DMA requests after each. This would have been fine if not for CubeMX's insertion of an interrupt upon every DMA request. You can't configure this from CubeMX, and I honestly don't know why they do it, especially if you select continuous conversion – it basically defeats the purpose of using DMA. Once I removed the two lines shown in the figure below, though, DMA hummed along nicely in the background instead of interrupting the CPU every time it completed a transfer.

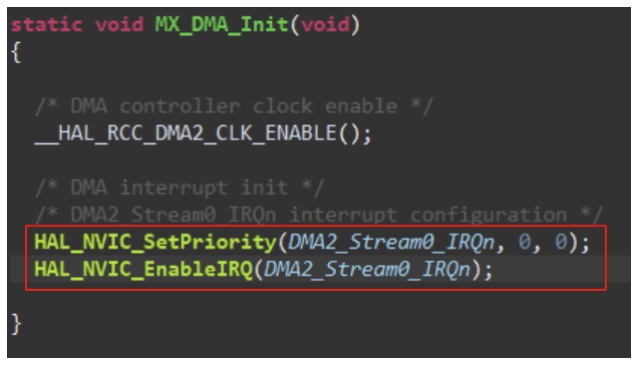
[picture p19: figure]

DMA interrupt inserted by CubeMX.

Note that these two lines will have to be commented out every time you generate code from CubeMX.

For triple-ADC operation, ADC1 works as a master and the other two work as slaves. See the figure below for the CubeMX setup I settled on for ADC1.

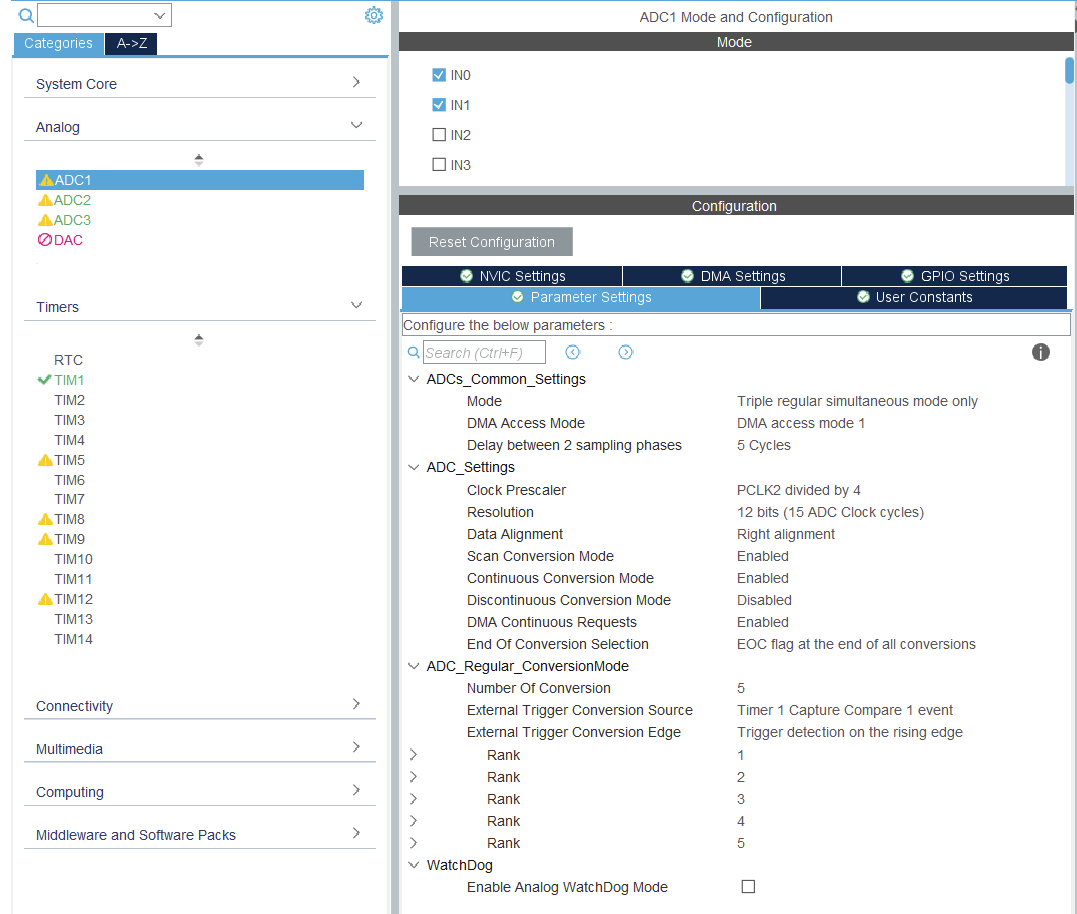
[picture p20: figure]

Prototype CubeMX setup for ADC1, which acts as master for ADC2 and ADC3.

### Pulse-width modulation

Pulse-width modulation is used to modulate current through a transistor while keeping it in its most efficient modes of operation – namely, not half-on. On the STM32F446, PWM capability is rolled into all generic timers, but more capability is present in the "Advanced timers", TIM1 and TIM8. These allow for complementary PWM outputs with inserted dead time, which is explicitly designed for half-bridge and motor control. The use of complementary PWM corresponds with the use of a 6PWM configuration on my custom board. The figure below shows the signals I wanted to produce using this peripheral.

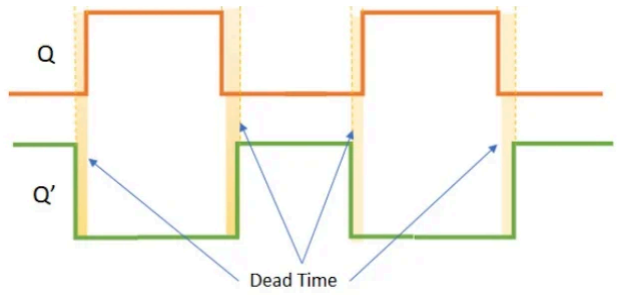
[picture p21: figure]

Complementary PWM outputs with inserted dead time. Source (https://www.allaboutcircuits.com/technical-articles/h-bridge-dc-motor-control-complementary-pulse-width-modulation-pwm-shoot-through-dead-time-pwm/)

This turned out to be surprisingly easy to set up and use: simply decide on a total PWM period, do the rest of the setup, and then update the duty cycle of the channel by directly writing to the CCR field in the main loop. The CubeMX setup for PWM generation is shown below.

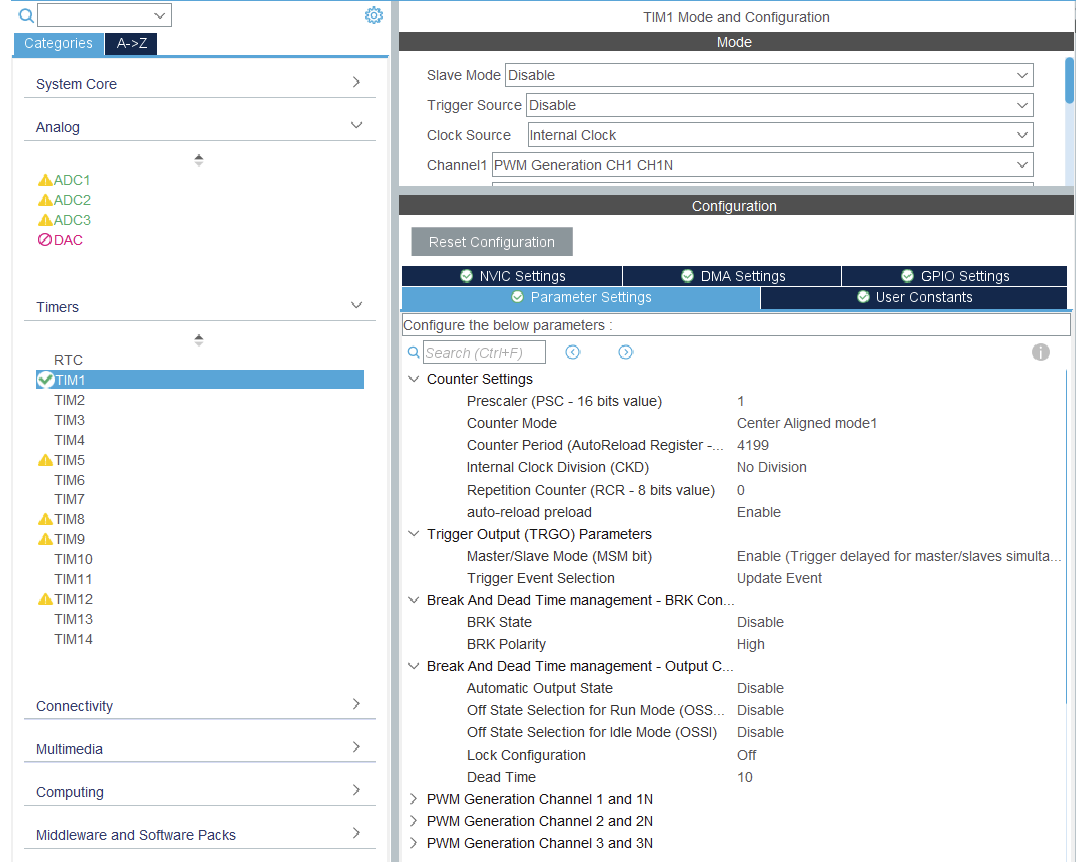
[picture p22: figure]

Prototype CubeMX setup for TIM1, which generates three complementary PWM channels.

With a prescalar of 1, a counter period of 4200 corresponds to a switching frequency of 1 kHz. This is super low for high-bandwidth control, but for the purposes of proving out the hardware, was perfectly fine. Center-aligned mode is very important for motor control as it leads to the proper overlapping of the phase PWM signals to produce torque. I am not exactly sure what would happen otherwise, but I am pretty sure it would at the very least be highly inefficient. A dead time of 1 us was used and is likely conservatively long. As a demonstration of how to update the duty cycle of each channel's PWM output, the figure below shows a snippet of my final position control code; see the last three lines where the CCRx fields are directly updated.

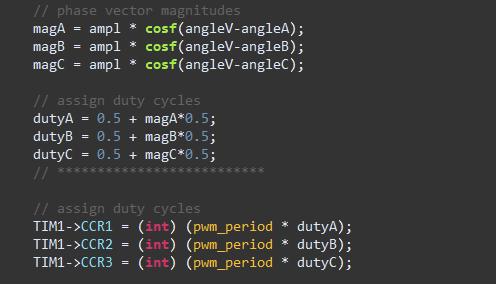
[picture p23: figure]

How to update the duty cycles of each PWM channel. Note dutyX values are in range [0,1].

With ADCs working and PWM set up, I could control an H-bridge to drive a DC motor at different speeds. A video of it in action is available here. (https://github.com/e36c/499-GaN/blob/master/non-code/media/half_bridge.MOV)

### Serial-peripheral interface

The last step to enable my first actual motor control program was to read motor position. For this I again relied on work done on the previous year's project and used the AS5147 on-axis magnetic SPI encoder IC to measure the angle of a diametrically-magnetized magnet mounted to the backside of a BLDC. Note that you don't need to know rotor position if you don't care to control rotor position, and you can instead use something like sensorless control which reads voltages off the motor phases to estimate rotor position. That wasn't a goal of this project so I opted to stay away from sensorless, at least for initial bringup.

Having used the AS5147 before, I knew its quirks. It exclusively uses 16-bit SPI transactions, but only sends 14-bit data, generating a parity bit for bit 14 and not even using bit 15 (the most significant bit). Simple masking did the trick for extracting the data I wanted, but the bigger challenge was getting the STM32 hardware abstraction layer (HAL) to read 16-bit data, as the main functions for SPI are meant for 8-bit data. The following figure shows the sort of casting required to use the HAL's pre-built SPI functions, as well as the masking required to extract the angle data from the encoder.

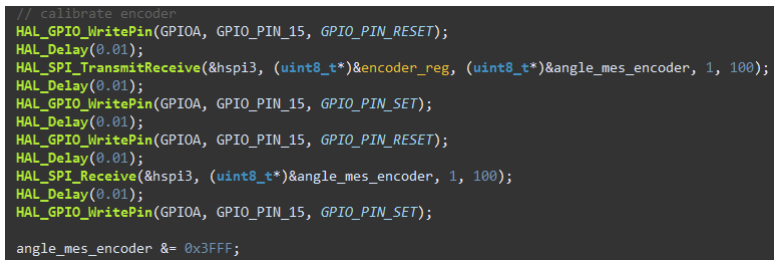
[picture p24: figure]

How to read angle data off of the AS5147 magnetic encoder IC via SPI.

In the end, this is a pretty simple part of the program. For pinout purposes, SPI3 was used. Luckily, the HAL doesn't make it too difficult to use any SPI block except for SPI1, like you might see with other microcontrollers or SPI libraries.

## Results

At the time of writing on June 11 2026, I have concluded work on this project for the quarter to allow myself to finish this report. I reached were basic position control then velocity control of a low-power (700W) BLDC motor. While I had originally aimed to achieve more advanced control, I am happy with this result and how I spent my time – methodically testing and layering on complexity slowly has given me full confidence that the foundations of this project are rock solid and will allow me to continue work towards more advanced control. I am proud of the hardware setup I have concluded the quarter with, as it contains everything I will need to make more progress. It is shown in the photo below.

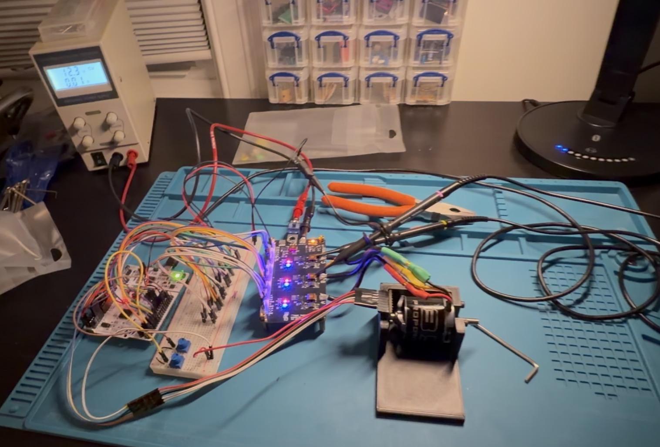
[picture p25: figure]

Hardware setup at the conclusion of this quarter.

The following sections detail the two modes of control I implemented.

### Position control

See this file (https://github.com/e36c/499-GaN/blob/master/ctrl_pos/Core/Src/main.c) for the position control code. This program is the culmination of every previous piece of firmware I had written: it reads all of the board's ADC values via DMA, commands complementary PWM values on the positive and negative halves of three TIM1 channels, and reads from a SPI encoder to determine motor position. As of the time of writing, the program uses a blocking SPI call; a perfect next step to speed up the main loop is to take advantage of the STM32's SPI DMA. The motor the code is set up for is a Propdrive v2 3542 1000KV BLDC, (https://hobbyking.com/en_us/propdrive-v2-3542-1000kv-brushless-outrunner-motor.html) a 17V 47A outrunner motor with 14 poles. I found this in the robotics lab and liked its high current rating, as it would use most of the 53A limit of the GaN chip when it came to torque control. After basic peripheral setup and initialization, the code works as follows:

1. Calibrate motor
1. Command some arbitrary, unbalanced duty cycle: Phase A is driven slightly positive, and phases B and C are driven slightly negative, bringing the motor angle to a stable position aligned with phase A
2. Wait a short while as the rotor settles
3. Read the encoder angle and assign it to the zero value, then return to balanced duty cycles to release the rotor
4. Assign electrical phase angles
1. Phase A angle = zero value
2. Phase B angle = zero value + 2π/3
3. Phase C angle = zero value + 4π/3
2. Position control loop

1. Read motor angle from encoder via 16-bit SPI transaction
2. Read potentiometer, assign to target angle
3. Calculate angle error, convert to electrical angle via motor pole count, then assign to amplitude of duty cycle via simple proportional controller
4. Calculate phase duty cycles
1. Find desired stator voltage electrical angle with ortho(rotor angle) in the direction that would produce torque in the desired direction
2. Take dot product of desired stator voltage electrical angle with rotor electrical angle
5. Write duty cycle values to PWM peripheral memory
6. Loop

There were several hiccups before I arrived at intuitive, spring-like behavior of the motor; it was through this process that I learned how to factor in electrical angle. The idea is that the stator coils repeat every so often as you move around the motor’s mechanical angle range. Selecting the number of stator coils and rotor magnets is an important decision that determines many motor properties. The number of times they repeat is indicated by the motor’s “pole count” as it’s often given. This means that while a certain rotor mechanical angle corresponds to a single electrical angle, a certain electrical angle could correspond to (pole pairs) amount of mechanical angles. So what we do is map the mechanical angle to the electrical angle it corresponds to, then deal only in that domain to do the remainder of the math. Before I realized that, I was repeatedly stumped by the variety of different stable points of the motor’s rotation not at the target angle, and its erratic behavior when applying external a torque to it. This behavior was due to the relationships between target encoder angle, measured encoder angle, and the output phase duty cycles being wonky due to the fact that I didn’t understand how to factor in rotor electrical angle, wrap angle error readings (so 6.27 rads was considered close to 0 rads), or which value of pole count to use. The solutions to those second two problems were to subtract or add multiples of pi/2 to bring the angle error within [-pi, pi], then to use the number of pole pairs, not total pole count, which was was 7 for our motor.

### Speed control

Speed control as I wrote it is very simple: simply add a certain amount to a target angle over time. So the system tracks a changing target angle. Pretty simple. See this video (https://github.com/e36c/499-GaN/blob/master/non-code/media/final_demo.MOV) for a final demo, showcasing position and speed control.

### Summary

The most impactful results include some of which I’ve already written about: the small things learned along the way that came from tackling subtle but often mighty problems. I went from messing up the setup of my first STM32CubeIDE project to stepping through compiled assembly and reading memory directly to determine the cause of a DMA problem; I started with no understanding of how bootstrapping a high-side FET works and ended up discovering organically why you can't indefinitely close it, solving an open question in my mind that had lasted since the bringup of the previous year's project; I went from knowing vaguely that the STM32 is "good for motor control" to understanding and actually implementing code that took advantage of its features. Most of all, this project gave me greater confidence in my ability to design good solid hardware and solve all sorts of problems during bringup, in hardware or software.

## Future work

The most obvious future work is to get vector control working. The good news is that all of the hardware is proven and much of the software basis is already written, and it should just be a matter of trying it and working through the bugs that pop up. The only big leap in the progression from position control to vector control is a more complex software control loop and the use of phase current readings, which are as yet untested at high current.

After that, any number of things could be the next steps:

- Speed up PWM, shorten dead time, and write as lightweight a control loop as possible to see how fast I can get it
- Find safe maximum board voltage, current, and power ratings
- Attempt sensorless, position-ignorant control using voltage measurements via high-frequency injection (HFI)
- Test overcurrent protection design
- Begin design of integrated driver board

I will use the findings from this project to design and develop a highly integrated motor drive, and I have full intention of continuing work on this project to get there.

## Conclusion

Thank you to Professor Alan Sahakian for making this project possible. without the ability to get credit for this effort, it would not have happened. His vast experience of designing and seeing so many low-level circuits lent itself well to the process of designing the hardware as well as beginning to understand the STM32’s peripherals, not to mention some great nerd conversations about measurement equipment and pacemakers. Thanks for being gracious even when I made you late to your dean meetings.

## Sources

In conjunction with lessons from my hands-on discoveries, the following sources helped me learn so much this past quarter.

- TBarkin121 on Github: GuardDog torque control code (https://github.com/Tbarkin121/GuardDog/blob/f4ff4e1f6701291bf12f183d5db0c924db871b79/stm32/MotorDrive/TorqueMode-10VV/Src/main.c)
- Switchcraft: Space Vector PWM Intro (https://www.switchcraft.org/learning/2017/3/15/space-vector-pwm-intro?rq=vector%20control) (incredibly helpful!)
- Nidec: Slot-pole combination (https://www.nidec.com/en/technology/motor/glossary/item/slot-pole_combination/)
- Teacher Sugiken's Motor Driver Dojo: What is a Brushless Motor? (https://techweb.rohm.com/product/motor/motor-library/comics/16370/)


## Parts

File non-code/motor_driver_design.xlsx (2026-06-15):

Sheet: BOM
Index | Description | Mfr | Mfr PN | Supplier | Supplier PN | Purchase link | Price | Qty needed | Total BOM cost (purchase more!)
 | 8p connectors | Molex | 0022272081 | DigiKey | WM4117-ND | https://www.digikey.com/en/products/detail/molex/0022272081/WM4117-ND/1130583 | $1.70 | 4 | $6.80
 | GaN half bridge | Texas Instruments | LMG2100R026VBNR | DigiKey | 296-LMG2100R026VBNRCT-ND | https://www.digikey.com/en/products/detail/texas-instruments/LMG2100R026VBNR/25811484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 | $12.15 | 3 | $36.45
 | Buffer | Texas Instruments | SN74AUP1G14DBVT | DigiKey | 296-41492-1-ND | https://www.digikey.com/en/products/detail/texas-instruments/SN74AUP1G14DBVT/1569036 | $0.92 | 3 | $2.76
 | Inverter | Texas Instruments | SN74LVC1G14DBVT | DigiKey | 296-26597-1-ND | https://www.digikey.com/en/products/detail/texas-instruments/SN74LVC1G14DBVT/1592006 | $0.83 | 3 | $2.49
 | Current sense amp G=100 | Texas Instruments | INA241A4QDRQ1 | DigiKey | 296-INA241A4QDRQ1CT-ND | https://www.digikey.com/en/products/detail/texas-instruments/INA241A4QDRQ1/23331461 | $3.89 | 3 | $11.67
 | Shunt resistor | Yageo | PU2726FKMPD0U3L | DigiKey | 13-PU2726FKMPD0U3LCT-ND | https://www.digikey.com/en/products/detail/yageo/PU2726FKMPD0U3L/25854094 | $1.70 | 4 | $6.80
 | Comparator | Rohm | BU7253F-E2 | DigiKey | BU7253F-E2CT-ND | https://www.digikey.com/en/products/detail/rohm-semiconductor/BU7253F-E2/5721133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 | $0.74 | 1 | $0.74
 | NMOS 180mA | Diodes Inc. | 2N7002A-7 | DigiKey | 2N7002A-7DICT-ND | https://www.digikey.com/en/products/detail/diodes-incorporated/2N7002A-7/3451498 | $0.21 | 1 | $0.21
 | PMOS 93A | Vishay Siliconix | SQM100P10-19L_GE3 | DigiKey | SQM100P10-19L_GE3CT-ND | https://www.digikey.com/en/products/detail/vishay-siliconix/SQM100P10-19L-GE3/7566797 | $4.71 | 1 | $4.71
 | Current sense amp G=50 | Texas Instruments | INA241A3IDR | DigiKey | 296-INA241A3IDRCT-ND | https://www.digikey.com/en/products/detail/texas-instruments/INA241A3IDR/22106764 | $3.45 | 1 | $3.45
 | 3.6V LDO | Texas Instruments | TLV70036DDCR | DigiKey | 296-40611-1-ND | https://www.digikey.com/en/products/detail/texas-instruments/TLV70036DDCR/3727089 | $0.23 | 1 | $0.23
 | 5V LDO | Microchip | MCP1792T-5002H/CBVAO | DigiKey | 150-MCP1792T-5002H/CBVAOCT-ND | https://www.digikey.com/en/products/detail/microchip-technology/MCP1792T-5002H-CBVAO/11481629 | $0.91 | 1 | $0.91
 | Zener 1.8V | onsemi | SZMMSZ4678T1G | DigiKey | SZMMSZ4678T1GOSCT-ND | https://www.digikey.com/en/products/detail/onsemi/SZMMSZ4678T1G/3063308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 | $0.11 | 4 | $0.44
 | Zener 3.0V | onsemi | SZBZX84C3V0ET1G | DigiKey | 488-SZBZX84C3V0ET1GCT-ND | https://www.digikey.com/en/products/detail/onsemi/SZBZX84C3V0ET1G/3536775 | $0.22 | 1 | $0.22
 | LED green | Harvatek Corporation | B1911NG--20D000214U1930 | DigiKey | 3147-B1911NG--20D000214U1930CT-ND | https://www.digikey.com/en/products/detail/harvatek-corporation/B1911NG-20D000214U1930/15519989 | $0.21 | 1 | $0.21
 | LED yellow | Harvatek Corporation | B1911UY--20D000114U1930 | DigiKey | 3147-B1911UY--20D000114U1930CT-ND | https://www.digikey.com/en/products/detail/harvatek-corporation/B1911UY-20D000114U1930/15519976 | $0.22 | 1 | $0.22
 | LED blue | Würth Elektronik | 150060BS55040 | DigiKey | 732-12013-1-ND | https://www.digikey.com/en/products/detail/w%C3%BCrth-elektronik/150060BS55040/8557178 | $0.19 | 3 | $0.57
 | LED red | Würth Elektronik | 150060SS55040 | DigiKey | 732-12016-1-ND | https://www.digikey.com/en/products/detail/w%C3%BCrth-elektronik/150060SS55040/8557181 | $0.19 | 3 | $0.57
 | Resistor 0R | Yageo |  | DigiKey | 311-0.0GRCT-ND | https://www.digikey.com/en/products/detail/yageo/RC0603JR-070RL/726675 | $0.10 | 5 | $0.50
 | Resistor 10k LOW % | Yageo |  | DigiKey | YAG1236CT-ND | https://www.digikey.com/en/products/detail/yageo/RT0603BRD0710KL/1072198 | $0.10 | 6 | $0.60
 | Resistor 130k LOW % | Yageo |  | DigiKey | YAG1521CT-ND | https://www.digikey.com/en/products/detail/yageo/RT0603BRD07130KL/1072234 | $0.10 | 5 | $0.50
 | Resistor 1k | Yageo |  | DigiKey | YAG1237CT-ND | https://www.digikey.com/en/products/detail/yageo/RT0603BRD071KL/1072344 | $0.10 | 7 | $0.70
 | Resistor 100R | Yageo |  | DigiKey | 311-100HRCT-ND | https://www.digikey.com/en/products/detail/yageo/RC0603FR-07100RL/726888 | $0.10 | 1 | $0.60
 | Resistor 200R | Yageo |  | DigiKey | 311-200HRCT-ND | https://www.digikey.com/en/products/detail/yageo/RC0603FR-07200RL/727043 | $0.10 | 3 | $0.50
 | Resistor 330R | Yageo |  | DigiKey | 311-330HRCT-ND | https://www.digikey.com/en/products/detail/yageo/RC0603FR-07330RL/727162 | $0.10 | 4 | $0.70
 | Capacitor 2.2uF 100V 0805 | Murata Electronics | GRM21BD72A225ME01K | DigiKey | 490-GRM21BD72A225ME01KCT-ND | https://www.digikey.com/en/products/detail/murata-electronics/GRM21BD72A225ME01K/15972575 | $0.27 | 10 | $2.69
 | Capacitor 2.2uF 16V 0603 | Samsung Electro-Mechanics | CL10A225KO8NNNC | DigiKey | 1276-1040-1-ND | https://www.digikey.com/en/products/detail/samsung-electro-mechanics/CL10A225KO8NNNC/3886698 | $0.10 | 4 | $0.40
 | Capacitor 0.1uF 16V 0402 | Murata | GCM155R71C104KA55J | DigiKey | 490-7998-1-ND | https://www.digikey.com/en/products/detail/murata-electronics/GCM155R71C104KA55J/2591252 | $0.03 | 15 | $0.43
 | Capacitor 1uF 16V 0402 | Samsung Electro-Mechanics | CL05A105KO5NNNC | DigiKey | 1276-1067-1-ND | https://www.digikey.com/en/products/detail/samsung-electro-mechanics/CL05A105KO5NNNC/3886725 | $0.10 | 6 | $0.60
 | Capacitor 10uF 100V alum | Nichicon | UUX2A100MNL1GS | DigiKey | 493-6279-1-ND | https://www.digikey.com/en/products/detail/nichicon/UUX2A100MNL1GS/2550555 | $0.57 | 6 | $3.42
 |  |  |  |  |  |  |  | Total: | $91.09

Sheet: Parts Order
Index | Refs | Description | Mfr | Mfr PN | Supplier | Supplier PN | Purchase link | Price | Qty buying | Total BOM cost (purchase more!) | Note
 | J1, J2, J3, J4 | 8p connectors | Molex | 0022272081 | DigiKey | WM4117-ND | https://www.digikey.com/en/products/detail/molex/0022272081/WM4117-ND/1130583 | $0.52 | 10 | $5.24
 | U1 | GaN half bridge | Texas Instruments | LMG2100R026VBNR | DigiKey | 296-LMG2100R026VBNRCT-ND | https://www.digikey.com/en/products/detail/texas-instruments/LMG2100R026VBNR/25811484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 | $13.00 | 5 | $65.00
 | U2 | Buffer | Texas Instruments | SN74AUP1G14DBVT | DigiKey | 296-41492-1-ND | https://www.digikey.com/en/products/detail/texas-instruments/SN74AUP1G14DBVT/1569036 | $0.92 | 6 | $5.52 | ^
 | U3 | Inverter | Texas Instruments | SN74LVC1G14DBVT | DigiKey | 296-26597-1-ND | https://www.digikey.com/en/products/detail/texas-instruments/SN74LVC1G14DBVT/1592006 | $0.83 | 6 | $4.98 | More expensive than the smaller chip (DRLR suffix), but will be easier to solder. Worth it for prototype 1.
 | U4 | Current sense amp G=100 | Texas Instruments | INA241A4QDRQ1 | DigiKey | 296-INA241A4QDRQ1CT-ND | https://www.digikey.com/en/products/detail/texas-instruments/INA241A4QDRQ1/23331461 | $4.00 | 6 | $24.00
 | R1, R8 | Shunt resistor | Yageo | PU2726FKMPD0U3L | DigiKey | 13-PU2726FKMPD0U3LCT-ND | https://www.digikey.com/en/products/detail/yageo/PU2726FKMPD0U3L/25854094 | $1.70 | 2 | $3.40 | Only 2 available to ship immediately from DK :(
 | U5 | Comparator | Rohm | BU7253F-E2 | DigiKey | BU7253F-E2CT-ND | https://www.digikey.com/en/products/detail/rohm-semiconductor/BU7253F-E2/5721133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 | $0.74 | 3 | $2.22
 | IC1 | NMOS 180mA | Diodes Inc. | 2N7002A-7 | DigiKey | 2N7002A-7DICT-ND | https://www.digikey.com/en/products/detail/diodes-incorporated/2N7002A-7/3451498 | $0.21 | 3 | $0.63
 | Q1 | PMOS 93A | Vishay Siliconix | SQM100P10-19L_GE3 | DigiKey | SQM100P10-19L_GE3CT-ND | https://www.digikey.com/en/products/detail/vishay-siliconix/SQM100P10-19L-GE3/7566797 | $4.71 | 2 | $9.42
 | U6 | Current sense amp G=50 | Texas Instruments | INA241A3IDR | DigiKey | 296-INA241A3IDRCT-ND | https://www.digikey.com/en/products/detail/texas-instruments/INA241A3IDR/22106764 | $3.45 | 2 | $6.90
 | U8 | 3.6V LDO | Texas Instruments | TLV70036DDCR | DigiKey | 296-40611-1-ND | https://www.digikey.com/en/products/detail/texas-instruments/TLV70036DDCR/3727089 | $0.24 | 3 | $0.72
 | U9 | 5V LDO | Microchip | MCP1792T-5002H/CBVAO | DigiKey | 150-MCP1792T-5002H/CBVAOCT-ND | https://www.digikey.com/en/products/detail/microchip-technology/MCP1792T-5002H-CBVAO/11481629 | $0.91 | 3 | $2.73
 | D3, D5 | Zener 1.8V | onsemi | SZMMSZ4678T1G | DigiKey | SZMMSZ4678T1GOSCT-ND | https://www.digikey.com/en/products/detail/onsemi/SZMMSZ4678T1G/3063308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 | $0.21 | 10 | $2.11
 | D4 | Zener 3.0V | onsemi | SZBZX84C3V0ET1G | DigiKey | 488-SZBZX84C3V0ET1GCT-ND | https://www.digikey.com/en/products/detail/onsemi/SZBZX84C3V0ET1G/3536775 | $0.22 | 2 | $0.44
 | D6 | LED green | Harvatek Corporation | B1911NG--20D000214U1930 | DigiKey | 3147-B1911NG--20D000214U1930CT-ND | https://www.digikey.com/en/products/detail/harvatek-corporation/B1911NG-20D000214U1930/15519989 | $0.14 | 10 | $1.45
 | D7 | LED yellow | Harvatek Corporation | B1911UY--20D000114U1930 | DigiKey | 3147-B1911UY--20D000114U1930CT-ND | https://www.digikey.com/en/products/detail/harvatek-corporation/B1911UY-20D000114U1930/15519976 | $0.15 | 10 | $1.53
 | D1 | LED blue | Würth Elektronik | 150060BS55040 | DigiKey | 732-12013-1-ND | https://www.digikey.com/en/products/detail/w%C3%BCrth-elektronik/150060BS55040/8557178 | $0.17 | 10 | $1.73
 | D2 | LED red | Würth Elektronik | 150060SS55040 | DigiKey | 732-12016-1-ND | https://www.digikey.com/en/products/detail/w%C3%BCrth-elektronik/150060SS55040/8557181 | $0.17 | 10 | $1.73
 | R24, R3 | Resistor 0R | Yageo |  | DigiKey | 311-0.0GRCT-ND | https://www.digikey.com/en/products/detail/yageo/RC0603JR-070RL/726675 | $0.01 | 25 | $0.20 | 3 for phases (LI cxn), 1 for OCP, 1 for shield cxn
 |  | Resistor 10k LOW % | Yageo |  | DigiKey | YAG1236CT-ND | https://www.digikey.com/en/products/detail/yageo/RT0603BRD0710KL/1072198 | $0.06 | 25 | $1.57 | 3 for phases, 3 for DC
 |  | Resistor 130k LOW % | Yageo |  | DigiKey | YAG1521CT-ND | https://www.digikey.com/en/products/detail/yageo/RT0603BRD07130KL/1072234 | $0.06 | 25 | $1.57 | 1 for each Vsense, 1 for OCP 0V6 ref
 |  | Resistor 1k | Yageo |  | DigiKey | YAG1237CT-ND | https://www.digikey.com/en/products/detail/yageo/RT0603BRD071KL/1072344 | $0.06 | 25 | $1.57 | 3 for phases, 4 for DC
 | C4, C5, C6 | Capacitor 2.2uF 100V 0805 | Murata Electronics | GRM21BD72A225ME01K | DigiKey | 490-GRM21BD72A225ME01KCT-ND | https://www.digikey.com/en/products/detail/murata-electronics/GRM21BD72A225ME01K/15972575 | $0.27 | 20 | $5.38 | 9 for phases, 1 for 5vreg
 | C1 | Capacitor 2.2uF 16V 0603 | Samsung Electro-Mechanics | CL10A225KO8NNNC | DigiKey | 1276-1040-1-ND | https://www.digikey.com/en/products/detail/samsung-electro-mechanics/CL10A225KO8NNNC/3886698 | $0.05 | 10 | $0.48 | 3 for phases, 1 on output of 5Vreg
 | C2, C3, C7, C9, C10, C15, C13, C16, C17 | Capacitor 0.1uF 16V 0402 | Murata | GCM155R71C104KA55J | DigiKey | 490-7998-1-ND | https://www.digikey.com/en/products/detail/murata-electronics/GCM155R71C104KA55J/2591252 | $0.02 | 50 | $1.04 | 9 for phases, 6 on DC
 | C8 | Capacitor 1uF 16V 0402 | Samsung Electro-Mechanics | CL05A105KO5NNNC | DigiKey | 1276-1067-1-ND | https://www.digikey.com/en/products/detail/samsung-electro-mechanics/CL05A105KO5NNNC/3886725 | $0.04 | 20 | $0.72 | 3 for phases, 3 on DC
 |  | Capacitor 10uF 100V alum | Nichicon | UUX2A100MNL1GS | DigiKey | 493-6279-1-ND | https://www.digikey.com/en/products/detail/nichicon/UUX2A100MNL1GS/2550555 | $0.35 | 12 | $4.26 | 2 for each phase
 |  | Resistor 100R | Yageo |  | DigiKey | 311-100HRCT-ND | https://www.digikey.com/en/products/detail/yageo/RC0603FR-07100RL/726888 | $0.02 | 10 | $0.24 | LEDs
 |  | Resistor 200R | Yageo |  | DigiKey | 311-200HRCT-ND | https://www.digikey.com/en/products/detail/yageo/RC0603FR-07200RL/727043 | $0.02 | 10 | $0.24 | LEDs
 |  | Resistor 330R | Yageo |  | DigiKey | 311-330HRCT-ND | https://www.digikey.com/en/products/detail/yageo/RC0603FR-07330RL/727162 | $0.02 | 10 | $0.24 | LEDs
 |  |  |  |  |  |  |  |  | Total: | $157.26

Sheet: Current Sensing
Current sensing: INA241
 |  |  |  | Notes
Max phase current | 53 | A, +/- | Set | Set by GaN chip, 2.6mOhm now
Shunt resistor value | 0.3 | mOhm | Variable
Shunt resistor power rating | 11 | W | Variable
Shunt tolerance | 1 | %
Shunt resistor max | 0.303 | mOhm | Worst-case calcs here only account for shunt R variation
Shunt resistor min | 0.297 | mOhm
Max shunt power (nom) | 0.8427 | W | Output | Not even close to a problem. Deciding factor became low gain for using as much ADC range as possible.
*max | 0.8511 | W | Output
*min | 0.8343 | W | Output
Shunt V at max I (nom) | 0.0159 | V | Output
*max | 0.0161 | V | Output
*min | 0.0157 | V | Output
INA241 supply V | 3.6 | V | Set
INA241 V reference | 1.8 | V | Set
INA241 gain | 100 | V/V | Variable | Options: 10, 20, 50, 100, 200
INA241 output swing (nom) | 1.59 | V, +/- | Output
*max | 1.6059
INA241 max output (nom) | 3.39
*max | 3.4059
INA241 min output (nom) | 0.21
*min | 0.1941
ADC supply V | 3.6 | V
ADC analog input range | 0V to above
Good shunt options
* Gain=100: https://www.digikey.com/en/products/detail/isabellenhuette-usa/BVN-Z-R0003-1-0/16733155
* G=20: 1.5mOhm, but power rating is too small for the one Bourns part that exists on DK
>> Tried for a while couldn't make this work. None exist on DK.
CURRENT SENSE BOM:
*INA2421A4 | https://www.digikey.com/en/products/detail/texas-instruments/INA241A4QDRQ1/23331461 | A4 = G=100. Automotive
*Shunt: PU2726 | https://www.digikey.com/en/products/detail/yageo/PU2726FKMPD0U3L/25854094 | Great, also automotive

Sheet: OCP PMOS Vgs
Supply voltage | 48 | V
PMOS Cgs | 13.50 | nF | max
NMOS max I | 0.18 | A
PMOS Vth | -2.5 | V | max
R14 value (ohm) | RC (us) | Leakage (A) | * This table assumes R14=R16, which is not the case - just a rough look at RC and leakage.
10000 | 135.00 | 0.0024
5000 | 67.50 | 0.0048
1000 | 13.50 | 0.024
500 | 6.75 | 0.048 | * I think I like this. NMOS should be fine carrying this leakage, and response time is 20x faster.
200 | 2.70 | 0.12
100 | 1.35 | 0.24
50 | 0.68 | 0.48
20 | 0.27 | 1.2
10 | 0.14 | 2.4
5 | 0.07 | 4.8
Final choice
R14 | R16 | Vdiv ratio | Vgs | RC (us) | Leakage (A)
470 | 1000 | 0.6802721088 | -15.34693878 | 6.345 | 0.033
330 | 1000 | 0.7518796992 | -11.90977444 | 4.455 | 0.036 | * Final choice. Solidly on, solidly fast, won't stress PMOS too much (only 60% of max Vgs), leakage not a problem.
220 | 1000 | 0.8196721311 | -8.655737705 | 2.970 | 0.039
100 | 1000 | 0.9090909091 | -4.363636364 | 1.350 | 0.044
47 | 1000 | 0.9551098376 | -2.154727794 | 0.634 | 0.046

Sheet: Motor Selection
Mfr | Name | Price | Link | Max current (A) | Rated V (V) | Max power (W) | Notes
Hobbywing | M4006 Light |  | https://www.hobbywing.com/en/products/m4006ul | 17.3 | 24 | 358 | Small motor, but $40.
T-Motor | U8 Lite L |  | https://uav-en.tmotor.com/2020/u_0930/373.html | 38 | 48 | 1790
Hobbywing | Skateboard Motor |  | https://www.hobbywing.com/en/products/orangered-skateboard-motor156
Hobbywing | M6208 |  | https://www.hobbywingdirect.com/products/xrotor-m-6208-motor-ul?pr_prod_strat=e5_desc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 |  | 48 | 250 | Doesn't state current, but recommends 60A ESC
Hobbywing | V5212 275KV | $70 | https://www.hobbywing.com/en/products/hv5212275kv | 53 | 48 | 2469 | Damn this might be the one except it is too small. $70
Hobbywing | V6212 180KV |  | https://www.hobbywing.com/en/products/hv6215210kv | 58 | 48 | 2685 | OK EXCEPT UNKNOWN WHERE TO BUY… Okay this actually might be the one. 68mm dia is workable, and I like the protected part.
Hobbywing | M6210 320 KV | $90 | https://www.hobbywing.com/en/products/hm6210hp | 55.2 | 24 | 1270 | Few different KVs for this that might work. Pretty good size, and nicely protected is a plus.
Hobbywing | M8108 100 KV | $130 | https://www.hobbywing.com/en/products/m8108 | 34.3 | 48 | 1572 | High protection again. Similar unprotected sold for same price
 | Conclusions
 | *Can get a pretty solid motor, spec-wise, for ~$100
 | *Not sure about quality of Hobbywing's stuff
 | *I like high protection version of Hobbywing's stuff - cleaner overall package, more versatile use
 | *There's no reason not to max out the capability of the GaN chip - 53A. = resize shunt.

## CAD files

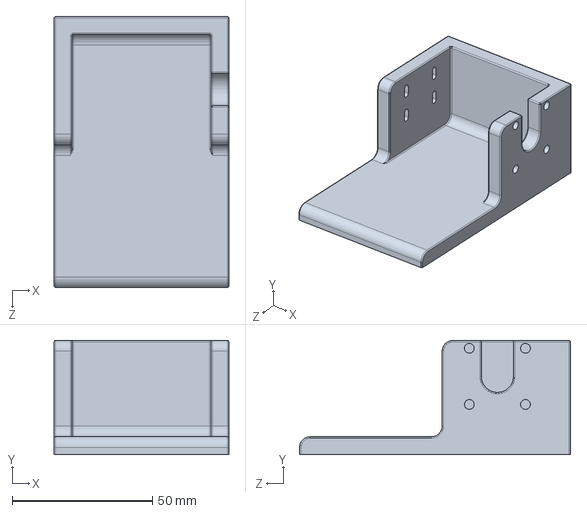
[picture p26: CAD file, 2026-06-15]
non-code/motor_mount.SLDPRT
62.2 x 40.6 x 96.5 mm

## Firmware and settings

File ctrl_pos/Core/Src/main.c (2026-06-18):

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
/* Includes ------------------------------------------------------------------*/
#include "main.h"

/* USER CODE BEGIN Includes */
#include <stdio.h>
#include <math.h>
/* USER CODE END Includes */

/* USER CODE BEGIN PD */
#define PUTCHAR_PROTOTYPE 		int __io_putchar(int ch)
#define PI						3.14159265358979
#define ENC2RADS				2.0*PI / 16383.0
#define POLE_PAIRS				7
#define THRESH_CTRL				0.005
/* USER CODE END PD */

ADC_HandleTypeDef hadc1;
ADC_HandleTypeDef hadc2;
ADC_HandleTypeDef hadc3;
DMA_HandleTypeDef hdma_adc1;

SPI_HandleTypeDef hspi3;

TIM_HandleTypeDef htim1;

/* USER CODE BEGIN PV */
uint32_t adc_dma_buf[15];

uint16_t angle_mes_encoder;
float angle_mes;
float angle_tgt;
float angle_err;
float angle_not;
float angle_elec;

int i = 0;
int t = 0;

float ampl = 0;
float drive_freq = 0;

float dutyA = 0.5;
float dutyB = 0.5;
float dutyC = 0.5;

float adc12 = 0;

float magA;
float magB;
float magC;
float angleA;
float angleB;
float angleC;
float angleV;

// GAINS
float gain_p = 0.1;

/* USER CODE END PV */

void SystemClock_Config(void);
static void MX_GPIO_Init(void);
static void MX_DMA_Init(void);
static void MX_ADC1_Init(void);
static void MX_ADC2_Init(void);
static void MX_ADC3_Init(void);
static void MX_TIM1_Init(void);
static void MX_SPI3_Init(void);
/**
  * @brief  The application entry point.
  * @retval int
  */
int main(void)
{

  /* MCU Configuration--------------------------------------------------------*/

  /* Reset of all peripherals, Initializes the Flash interface and the Systick. */
  HAL_Init();

  /* Configure the system clock */
  SystemClock_Config();

  /* Initialize all configured peripherals */
  MX_GPIO_Init();
  MX_DMA_Init();
  MX_ADC1_Init();
  MX_ADC2_Init();
  MX_ADC3_Init();
  MX_TIM1_Init();
  MX_SPI3_Init();
  /* USER CODE BEGIN 2 */
  HAL_TIM_PWM_Start(&htim1, TIM_CHANNEL_1);
  HAL_TIMEx_PWMN_Start(&htim1, TIM_CHANNEL_1);
  HAL_TIM_PWM_Start(&htim1, TIM_CHANNEL_2);
  HAL_TIMEx_PWMN_Start(&htim1, TIM_CHANNEL_2);
  HAL_TIM_PWM_Start(&htim1, TIM_CHANNEL_3);
  HAL_TIMEx_PWMN_Start(&htim1, TIM_CHANNEL_3);

  HAL_ADC_Start(&hadc2);
  HAL_ADC_Start(&hadc3);

  HAL_ADCEx_MultiModeStart_DMA(&hadc1, adc_dma_buf, 15);
  int pwm_period = TIM1->ARR;

  const uint16_t encoder_reg = 0x3FFF | 0x4000 | 0x8000; 	// reg | read | parity
  const uint16_t eerfl_reg = 0x0001 | 0x4000 | 0x8000;		// reg | read | parity

  /* USER CODE END 2 */

  /* Infinite loop */
  /* USER CODE BEGIN WHILE */

  // align motor to phase A
  dutyA = 0.52;
  dutyB = 0.48;
  dutyC = 0.48;

  TIM1->CCR1 = (int) (pwm_period * dutyA);
  TIM1->CCR2 = (int) (pwm_period * dutyB);
  TIM1->CCR3 = (int) (pwm_period * dutyC);

  HAL_Delay(2000);

  // calibrate encoder
  HAL_GPIO_WritePin(GPIOA, GPIO_PIN_15, GPIO_PIN_RESET);
  HAL_Delay(0.01);
  HAL_SPI_TransmitReceive(&hspi3, (uint8_t*)&encoder_reg, (uint8_t*)&angle_mes_encoder, 1, 100);
  HAL_Delay(0.01);
  HAL_GPIO_WritePin(GPIOA, GPIO_PIN_15, GPIO_PIN_SET);
  HAL_Delay(0.01);
  HAL_GPIO_WritePin(GPIOA, GPIO_PIN_15, GPIO_PIN_RESET);
  HAL_Delay(0.01);
  HAL_SPI_Receive(&hspi3, (uint8_t*)&angle_mes_encoder, 1, 100);
  HAL_Delay(0.01);
  HAL_GPIO_WritePin(GPIOA, GPIO_PIN_15, GPIO_PIN_SET);

  angle_mes_encoder &= 0x3FFF;
  angle_mes = angle_mes_encoder*ENC2RADS;	// measured angle is now in radians
  angle_not = angle_mes;	// "naught". zero position, in radians

  // clear PWM output
  TIM1->CCR1 = (int) 0;
  TIM1->CCR2 = (int) 0;
  TIM1->CCR3 = (int) 0;

  // phase angles
  angleA = angle_not;
  angleB = angle_not + PI/1.5;	// *2pi/3
  angleC = angle_not + PI/0.75;	// *4pi/3

  while (1)
  {


	// change angle with pots
	adc12 = 0.3*adc_dma_buf[12] + 0.7*adc12;

	if (adc_dma_buf[0] < 3000) {	// position control mode
		angle_tgt = 0.5 * (2*PI*((float) adc12) / 4095.0);
	}
	else {							// bonus speed control mode!
		angle_tgt += 0.2 * ((float) adc12) / 4095.0;
	}

	// retrieve rotor position
	HAL_GPIO_WritePin(GPIOA, GPIO_PIN_15, GPIO_PIN_RESET);
	HAL_SPI_TransmitReceive(&hspi3, (uint8_t*)&encoder_reg, (uint8_t*)&angle_mes_encoder, 1, 100);
	HAL_GPIO_WritePin(GPIOA, GPIO_PIN_15, GPIO_PIN_SET);
	angle_mes = (angle_mes_encoder & 0x3FFF) * ENC2RADS;

	// ******control position******
	// error
	angle_err = angle_tgt - angle_mes;	// rads
	if (angle_err>0) 	angle_err=fmodf(angle_err+PI,2*PI)-PI;
	else				angle_err=fmodf(angle_err-PI,2*PI)+PI;	// caps angle_err to (-pi,pi)

	// amplitude of voltage vector
	ampl = fabs(gain_p*angle_err);
	if (ampl>1) ampl = 1;

	// angle of voltage vector - set 90deg
	angle_elec = POLE_PAIRS*angle_mes + angle_not;
	angleV = angle_elec + PI/2.0*(angle_err>THRESH_CTRL) - PI/2.0*(angle_err<-THRESH_CTRL);	// orthogonal torque vector

	// phase vector magnitudes
	magA = ampl * cosf(angleV-angleA);
	magB = ampl * cosf(angleV-angleB);
	magC = ampl * cosf(angleV-angleC);

	// assign duty cycles
	dutyA = 0.5 + magA*0.5;
	dutyB = 0.5 + magB*0.5;
	dutyC = 0.5 + magC*0.5;
	// **************************

	// assign duty cycles
    TIM1->CCR1 = (int) (pwm_period * dutyA);
    TIM1->CCR2 = (int) (pwm_period * dutyB);
    TIM1->CCR3 = (int) (pwm_period * dutyC);

//    HAL_Delay(0.01);
    /* USER CODE END WHILE */

    /* USER CODE BEGIN 3 */
  }
  /* USER CODE END 3 */
}

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


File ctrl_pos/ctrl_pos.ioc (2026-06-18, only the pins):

Mcu.UserName=STM32F446RETx
PA0-WKUP.Signal=ADCx_IN0
PA1.Signal=ADCx_IN1
PA10.Signal=S_TIM1_CH3
PA13.GPIO_Label=TMS
PA13.Signal=SYS_JTMS-SWDIO
PA14.GPIO_Label=TCK
PA14.Signal=SYS_JTCK-SWCLK
PA15.Signal=GPIO_Output
PA2.Signal=ADCx_IN2
PA3.Signal=ADCx_IN3
PA4.Signal=ADCx_IN4
PA5.Signal=ADCx_IN5
PA6.Signal=ADCx_IN6
PA7.Signal=ADCx_IN7
PA8.Signal=S_TIM1_CH1
PA9.Signal=S_TIM1_CH2
PB13.Signal=TIM1_CH1N
PB14.Signal=TIM1_CH2N
PB15.Signal=TIM1_CH3N
PB3.GPIO_Label=SWO
PB3.Signal=SYS_JTDO-SWO
PC0.Signal=ADCx_IN10
PC1.Signal=ADCx_IN11
PC10.Signal=SPI3_SCK
PC11.Signal=SPI3_MISO
PC12.Signal=SPI3_MOSI
PC13.GPIO_Label=B1 [Blue PushButton]
PC13.Signal=GPXTI13
PC14-OSC32_IN.Signal=RCC_OSC32_IN
PC15-OSC32_OUT.Signal=RCC_OSC32_OUT
PC2.Signal=ADCx_IN12
PC3.Signal=ADCx_IN13
PC4.Signal=ADCx_IN14
PC5.Signal=ADCx_IN15
PH0-OSC_IN.Signal=RCC_OSC_IN
PH1-OSC_OUT.Signal=RCC_OSC_OUT

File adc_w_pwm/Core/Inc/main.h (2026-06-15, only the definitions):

#define B1_Pin GPIO_PIN_13
#define B1_GPIO_Port GPIOC
#define TMS_Pin GPIO_PIN_13
#define TMS_GPIO_Port GPIOA
#define TCK_Pin GPIO_PIN_14
#define TCK_GPIO_Port GPIOA
#define SWO_Pin GPIO_PIN_3
#define SWO_GPIO_Port GPIOB

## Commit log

2026-06-17 increased switching speed
2026-06-18 sped up everything: clock, angle wrap calc, motor
2026-06-19 added README, ecad, board render
    [dc_sense.SchDoc, motor_driver499.PrjPcb, phase.SchDoc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]

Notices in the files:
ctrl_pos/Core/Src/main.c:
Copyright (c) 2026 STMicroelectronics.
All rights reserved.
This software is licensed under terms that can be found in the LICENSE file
